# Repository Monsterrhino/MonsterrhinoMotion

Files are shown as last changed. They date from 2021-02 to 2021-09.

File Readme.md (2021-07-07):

# MonsterrhinoMotion

## Introduction
The MonsterrhinoMotion card is an independent stepper motor driver card to power and control up to 4 stepper motors that comes with a pre-installed firmware. The MonsterrhinoMotion card uses high quality stepper drivers (TMC5160) from Trinamic.
You can use Monsterrhino Motion in different ways depending on the complexity of your project: 

- Use the pre-installed library by sending commands **over a serial USB port** using a variety of predefined functions (see below)
- Use the pre-installed library by sending commands **over CAN bus** using a variety of predefined functions (see in the MonsterrhinoControl documentation)
- Program functions and actions with the **provided Arduino library** and upload directly to the card

In the simplest case all you need to do is **just connect 24V, a stepper motor and a USB cable** to the Monsterrhino Motion and you are ready to move the motor - **plug and play**.

The key features of the MonsterrhinoMotion stepper driver card are:

- up to 4 stepper motors
- two limit switches per motor
- encoder for each stepper motor
- up 12 digital inputs (24V)
- 1 digital output (24V)
- 3 PWM outputs (open collector)
- 2 CAN bus connector 
- USB C connector
- micro USB connector
- analog emergency power-off circuit that can be bridged with a jumper

## MonsterrhinoMotion pinout

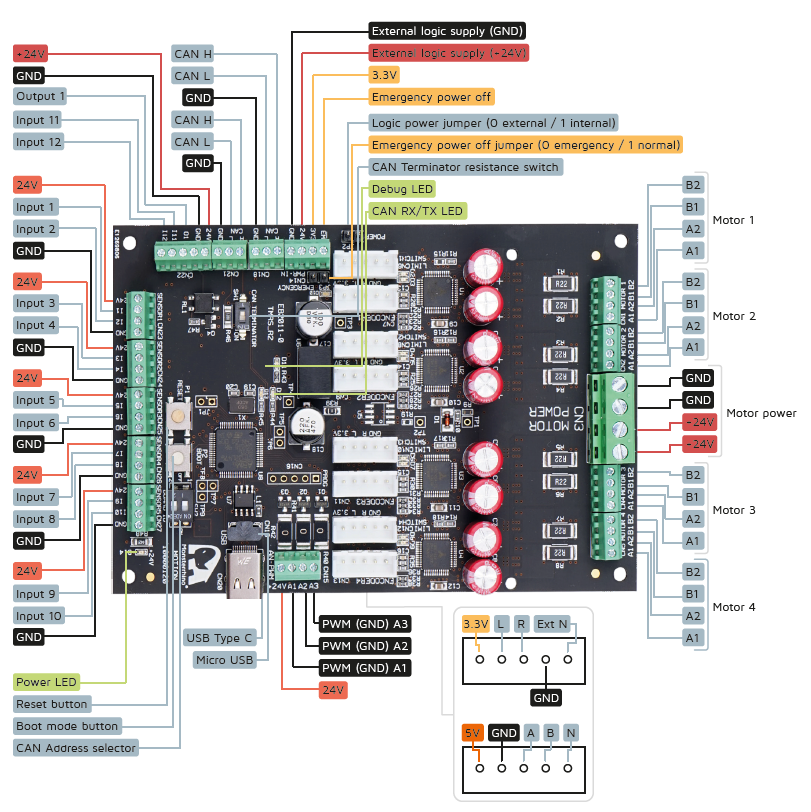
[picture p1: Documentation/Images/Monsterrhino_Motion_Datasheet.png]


## USB serial communication

### Connect to Monsterrhino Motion

Install the Arduino IDE on your computer (https://www.arduino.cc/en/software). Open the Arduino IDE on your computer. 

+ Select the right port under **Tools->Port** e.g. /dev/ttyACM0 or COM5. 
+ Open the serial monitor and set **115200 baud** and line ending to **Both NL & CR**. 

  <br><br>
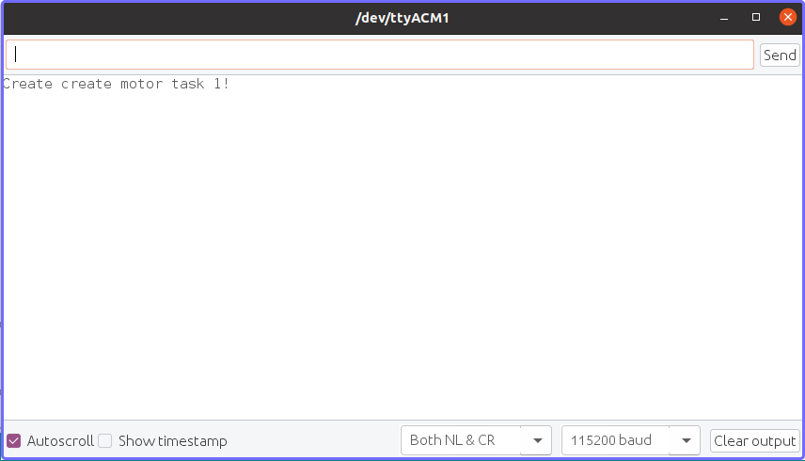
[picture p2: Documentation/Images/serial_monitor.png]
   
  <br><br>

Press the reset button on the Monsterrhino Motion than your ready to type your first command. If you have Motor 1 connected you can for example type: **m1mr 100** into the serial monitor and hit enter - now Motor 1 should move 1000 steps (that is 5 rotations - 200 steps per rotation or 1.8° per step). The meaning of this command is: **m1** - motor 1, **mr** move relative, **1000** - hundred steps. With **m1mr -1000** you can move 1000 steps into the other direction. 

(http://www.youtube.com/watch?v=Wm-6o_nRb1g "Serial communication")

### Commands
The MonsterrhinoMotion commands are combinations of commands from the list below. They are composed of the classifier: **m, i or f**. A number after the classifier letter selects the desired motor, input, or function: Motor 1 = **m1**, Userfunction 1 = **f1**. The classifier is followed by a function such as targetposition = **tp** and a number.

- **m1tp 100** - motor 1 move to target position 100
- **m4ma 200** - motor 4 set motor current to 200 mA
- **m3smp** - motor 3 save motor parameters
- **m2cp ?** - request motor 2 current position

The questionmark can generally be used to request a current value e.g. Motor 1 what is the current position = **m1tp ?**.

motor function |**subfunction**    |**subfunction** | values
---         | :-:     | :-: | :-:
TargetPosition |tp|targetpos |
CurrentPosition|cp|currentpos|
Rampmode|rm|rampmode |	p or positioning, v or velocity, h or hold
Motor current|ma|currentma |
MaxSpeed|ms|maxspeed |
CurrentSpeed|cs|currentspeed|
Register|r|register|
RampSpeeds|rs|rampspeeds|
Acceleration|ac|acceleration|
Accelerations|as|accelerations|
Stop|s|stop|
Enable|en|enable|
Disable|di|disable|
EncoderPosition|ep|encoderposition |
LatchedPosition|lp|latchedposition|
LatchedEncoderPosition|le|latchedencoder|
MotorDriveStatus|mds|motordrvstatus|
MotorRampStat|mrs|motorrampstat|
gStat|gs|gstat|
MotorCurrent|ma|currentma|
Freewheelingmode|fwm| freewheelingmode|
ModeChangeSpeeds|mcs| modechangespeeds|
Switch Mode|swm|swmode|
Save|sv|save|
SaveMotorParameter|smp|savemotorparameter|
Test|test|
Load|ld|load|
Startup|st|startup |

**input function**|subfunction|subfunction
---         | :-:     | :-:
InputFunction|if|inputfunction
StartUp|st|startup

**system function**|subfunction|subfunction
---         | :-:     | :-:
Start|s|start
Stop|t|stop
Variable|v|variable
Float|f|float
Startup|st|startup
Unlock|u|unlook

## Program the **Monsterrhinostep library** with Arduino IDE or VisualMicro

To use the the Monsterrhinosteb-Lib (https://github.com/Monsterrhino/MonsterrhinoMotion/tree/master/Library) library it is necessary to install following packages first:

## On Windows
Tested on Windows 10.

### Install Java Runtime Environment
If not already satisfied:

* Download the Java Runtime Environment from the official Website - https://www.java.com/en/download/manual.jsp 
* Install it by running the executable (.exe) file

### Prepare Arduino IDE:
* Download and install the Arduino IDE (Version 1.8.12) from the official page: https://www.arduino.cc/en/Main/Software (or get it from the Software folder)

* Start the Arduino IDE and add **Stm32duino** as follows:
  + Go to **File->Preferences**. Under the section **Additional Boards Manager URLs**:

       ```https://raw.githubusercontent.com/stm32duino/BoardManagerFiles/master/STM32/package_stm_index.json  ```  
       
**Note:** Please use exacatly this version, even if its deprecated
       
  <br><br>
  ![](Documentation/Images/additional_boards.png)     
  <br><br>
  
  + Go to **Tools->Board->Boards Manager** and search for **STM32 Cores**, choose version **1.8.0** and press *Install*. 
  
  <br><br>
  ![](Documentation/Images/boards_manager.png)    
  <br><br>
  
  After that you should be able to select **Nucleo-64** under **Tools->Board**. 

  <br><br>
  ![](Documentation/Images/nucleo64.png) 
  <br><br>
  
### Install STM32CubeProgrammer:
  
* Download **STM32CubeProgrammer** from the official page: https://www.st.com/en/development-tools/stm32cubeprog.html. You need to enter your email address for that. 
* Install it by running the executable (.exe) file.
* You can install it with the default settings. During the installation process, the drivers will be installed to.
* Verify the installation by opening the programm **STM32CubeProgrammer**. If the program opens normally, everything should be fine.

-----------------------------------------------------------------
**_Attention_:**
Check if you can open the **STM32CubeProgrammer** and connect to your MonsterrhinoMotion. Select USB and **bring your MonsterrhinoMotion into boot-mode** by pressing reset while holding down the boot button. After successfully connecting to your device you should see something similar to:

  <br><br>
  ![](Documentation/Images/stm32.png) 
  <br><br>

### Following files need to be replaced inside the Arduino folder
Replace following two files on your computer with the files you find inside the https://github.com/Monsterrhino/MonsterrhinoMotion/tree/master/Library/Replace folder:

  + Replace **usbd_cdc_if.c** inside:  
  ```C:\Users\username\AppData\Local\Arduino15\packages\STM32\hardware\stm32\1.8.0\cores\arduino\stm32\usb\cdc```
  **or**
  ```C:\Users\username\Documents\ArduinoData\packages\STM32\hardware\stm32\1.8.0\cores\arduino\stm32\usb\cdc ```  
   **-** depending on location of your installation (it could also be a different location). 
  
  + Replace **variant.c** inside:  
  ```C:\Users\username\AppData\Local\Arduino15\packages\STM32\hardware\stm32\1.8.0\variants\NUCLEO_L476RG ``` 
  **or**
  ```C:\Users\username\Documents\ArduinoData\packages\STM32\hardware\stm32\1.8.0\variants\NUCLEO_L476RG ```  
   **-** depending on location of your installation (it could also be a different location). 

### Add the **STM32duino_FreeRTOS.zip** to the Arduino IDE:
The **STM32duino_FreeRTOS.zip** can be found here: https://github.com/Monsterrhino/MonsterrhinoMotion/tree/master/Library. Download it and add **STM32duino_FreeRTOS.zip** to the Arduino IDE libraries from the menu **Sketch->Include Library->Add ZIP Library**.
  
### Add the **MonsterrhinoStep-Lib** to the Arduino IDE:
To add the **MonsterrhinoStep-Lib** to the Arduino IDE download the **MonsterrhinoStep-Lib.zip** from https://github.com/Monsterrhino/MonsterrhinoMotion/tree/master/Library and proceed with following steps:

* Open the Arduino IDE, for each libary inside the Libs folder go to **Sketch->IncludeLibrary->Add .ZIP Library ..** and select the **MonsterrhinoStep-Lib.zip** file.
* Open the Monsterrhino application in your Arduino IDE: **File->Examples->Monsterrhinostep->monsterrhinostep**.
  
  <br><br>
  ![](Documentation/Images/monsterrhinostep.png) 
  <br><br>
  
  Now you should see following files in the Arduino IDE: **monsterrhinostep**, **User_Functions1.cpp**, **User_Functions2.cpp**, **User_Functions3.cpp**, **User_Functions4.cpp**, **User_Functions5.cpp**, **User_Functions6.cpp**, **build_opt.h**.
  
  <br><br>
  ![](Documentation/Images/library.png) 
  <br><br>
  
* Before you can start you need to adjust some settings in the Arduino IDE under **Tools**:
  + Board: "Nucleo-64" **Tools -> Board .. -> STM32 Boards -> Nucleo-64**
  + Board part number: **Nucleo L476RG**
  + USB support (if available): **CDC (generic 'Serial' supersede U(S)ART-)**
  + Upload method: **STM32CubeProgrammer (DFU)** 
  
  <br><br>
  ![](Documentation/Images/settings.png) 
  <br><br>

### Upload your MonsterrhinoMostion application to your MonsterrhinoMotion card
  
For uploading a program, connect your computer to your MonsterrhinoMotion card via micro USB or USB C, push the reset button while holding down the debug button on your MonsterrhinoMotion card. You will hear the Windows USB connection sound twice. After successfully entering **boot mode** the debug LED will stop blinking.
Now you can hit the compile and upload button to upload the MonsterrhinoMotion application to the card. After the upload press the **reset button**.

### Set up Visual Studio to use with Monsterrhino
The setup of Arduino IDE shown before has to be completed prior to setting up Visual Studio.

* Download and install Visual Studio (https://docs.microsoft.com/en-us/visualstudio/install/install-visual-studio?view=vs-2019), add the workload **desktop development with c++** during the installation process. 
* Install Arduino Extension in Visual Studio: go to **Extension -> ManageExtensions -> Online**, search for **Arduino** and install **Arduino IDE for Visual Studio (Visual Micro)** (you will have to close Visual Studio during the installation process).
* Open the location configuration **Extensions -> vMicro -> General -> Configure Arduino IDE Location(s)** and enter the correct paths, it should look similar to the example in the image:  

<br><br>
![](Documentation/Images/config.jpg){width=50%}  
<br><br>

* Open VisualStudio and press **Continue without code** and then go to **File->Open->Arduino Project** and navigate to ```..\Arduino\libraries\Monsterrhinostep-Lib\examples\monsterrhinostep\monsterrhino.ino```
* Adjust the vMicro settings (**Extensions -> vMicro**) to the same values as you did in your Arduino IDE (see **adjust the Arduino IDE settings like follows** above)
* Open Visual Studio, open **Extensions -> vMicro -> ViewPortMonitor ** (Monsterrhino needs to be connected to your computer to be able to open it), switch the setting **line endings** to **Both CR & LF**
* You can now use the ViewPortMonitor to connect to your Monsterrhino and directly send commands 
* To use Visual Studio to compile and upload your code to your Monsterrhino, you first have to restart it in debug mode (keep debug button pushed while pressing the reset button)

## On Ubuntu 
Tested on Ubuntu 20.04. 

* Install the Arduino IDE (tested with version 1.8.12)
* In the Arduino IDE go to **Properties/Additional BoardsManager** and add following 

  ```https://github.com/stm32duino/BoardManagerFiles/raw/master/STM32/package_stm_index.json ```
  
* Under **Arduino/Boardsmanager** add ```stm32 cores```.
* Install the Java Runtime Environment by executing the following command in your terminal ```sudo apt install openjdk-8-jre```.
* Download and install the **STM32CubeProgrammer**. There might be problems with JavaFX, you can try this fix https://askubuntu.com/a/1316213.

  **Attention**
  Check if you can open the **STM32CubeProgrammer** and connect to your MonsterrhinoMotion. Select USB and bring your MonsterrhinoMotion into boot-mode by pressing reset while holding down the boot button. It might be usefull to open the **STM32CubeProgrammer** via the terminal, so you get some information if something is not right.
  
  **Note**
  If in your terminal you read something about **permission denied** it might be necessary to copy a rules.d file to the STM32 folder. To do so you can follow this instructions (taken from: https://community.st.com/s/question/0D53W000000aP9J/no-stm32-device-in-dfu-mode-connected): 
  
  * Make sure you have installed this library: ```sudo apt-get install libusb-1.0-0```
  * To allow STM32CubeProgrammer to access the USB port through low-level commands, proceed as follows: 
  ```cd $HOME/STM32MPU_workspace/STM32MPU-Tools/STM32CubeProgrammer-x.y.z/Drivers/rules```
  * Then execute: ```sudo cp *.* /etc/udev/rules.d/```
  * Restart the STM32CubeProgrammer 
  
  **After successfully connecting** to your device you should see something similar to:
  
    <br><br>
    ![](Documentation/Images/stm32.png) 
    <br><br>

* Replace following two files on your computer with the files you find inside the https://github.com/Monsterrhino/MonsterrhinoMotion/tree/master/Library/Replace     folder:

  + Replace **usbd_cdc_if.c** inside:  
  ``` /home/g/.arduino15/packages/STM32/hardware/stm32/1.8.0/cores/arduino/stm32/usb/cdc ```
  + Replace **variant.c** inside:  
  ``` /home/g/.arduino15/packages/STM32/hardware/stm32/1.8.0/variants/NUCLEO_L476RG ```
  
  * Add **Monsterrhinostep-Lib.zip** and **STM32duino_FreeRTOS.zip** to the Arduino IDE libraries from the menu **Sketch->Include Library->Add ZIP Library**.

* If you whant to use a **STM32nucleo** to program over **ST-Link** it might be necessary to give permission to the USB device (as described here: https://stackoverflow.com/questions/22713834/libusb-cannot-open-usb-device-permission-isse-netbeans-ubuntu): 
 ``` sudo chmod o+w /dev/bus/usb/123/456 ```

## Upload from STM32Cube

If you are not able to upload your project via the Arduino IDE you can try to upload the compiled project file with STM32Cube as follows:

* Compile your project in the Arduino IDE. Go to **->Sketch->Export compiled Binary**.

* Set your MonsterrhinoMotion in boot mode and connect it via STM32CubeProgrammer (see "Install STM32CubeProgrammer").

* Upload the compiled Hex-File to STM32CubeProgrammer with the task **->Open File** (next to Device memory).

* Press button **Download** to load your project to the device.

<br><br>
![](Documentation/Images/cubeProgrammer_upload.png) 
<br><br>

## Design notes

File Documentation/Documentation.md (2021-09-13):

---
title: "Monsterrhino Motion: Documentation and Examples"
output: 
  bookdown::html_document2:
    toc: true
    toc_float: true
    fig_caption: true
---
-->

<!-- ![](Images/Monsterrhino_Images/logo.png){width=20%} 

<p align="center">
  <img width="100" src="Images/Monsterrhino_Images/logo.png">
</p>

<p align="center">
  <img width="500" src="Images/Motion_Illustrated.png">
</p>
 -->
 
 <!-- 
 ![](Images/Reset_Boot.gif)
 
-->

# General
**Monsterrhino Motion** is an independent stepper motor controller.  

The MonsterrhinoMotion card can be controlled via three different ways: over **predefined USB commands**, over **predefined CAN commands** or by **programming the MonsterrhinoMotion card directly** using the Monsterrhinostep-Lib for the ArduinoIDE. 

It can run up to 4 stepper motors at once - in parallel. The powerful MCU combined with our advanced firmware (multitasking capable - up to 6 user tasks) allows you to control stepper motors in the most simple way - you can program it with the Arduino IDE or with more advanced IDEs. Our firmware allows you to program the card at a high level e.g. you tell the motor to rotate continuously, make a 100 steps, etc. Further key features are limit switch connectors for each motor, encoder connectors, digital sensor inputs and digital/analog outputs. 
The CAN interface offers reliable high performance communication with other devices such as Monsterrhino Motion, Monsterrhino Control, Raspberry Pi, Arduino and many more.

Specification:  

- **4** stepper motors
- **12** digital inputs
- **1** digital output (with load)
- **3** analog outputs
- **1** emergency jumper/switch

## Modes
As shown above, the Motion has two modes.  

-**Normal mode:** After a reset (press button P1 once) the Motion is in normal mode and the serial LED (D11) is blinking (existing USB-connection required).  
-**Boot mode:** This mode allows you to program the Motion.  

This animation shows you how to enter in these different modes:



## Communication
The board offers two main types of communication:  

* **Serial:** U(S)ART with USB is used to communicate with lower speed.
* **CAN:**  CAN (common in automotive) is used to communicate faster and without failure.

# USB
U(S)ART is the simplest way to give commands. MonsterrhinoMotion can be controlled directly, out of the box, via U(S)ART-communication.  

Just open the serial command window and select the following settings and the COM-port of your MonsterrhinoMotion.  
After a successful connection with your MonsterrhinoMotion you can send commands as shown here:  
(**Attention:** Motion needs to be in normal mode **not** boot mode! Led is blinking)
```
m1tp 100  (Motor 1 target point 100 steps)
m3mr 200  (Motor 3 move relative 200 steps)
m2ma 100  (Motor 2 set motor current to 100mA)

m3ma ?    (Motor 3 returns motor current in mA)
m2cp ?    (MOtor 2 returns current position)
```
**Note:** A list of all UART-commands can be found in the following chapter [Serial U(S)ART].

## Setup

### Arduino - Serial commands
First install the Arduino IDE on your computer. Open the Arduino IDE and connect the MonsterrhinoMotion card via USB cable. Supply the MonsterrhinoMotion with 24V, now you should see the green power indicator LED permanently shine. After plugin in the USB to the computer and pressing the Reset button on the MonsterrhinoMotion a second green LED should start blinking.

In the Arduino IDE select the port of your MonsterrhinoMotion, if the MonsterrhinoMotion is the only device you have connected to your computer you should see only one device in your list:
<br>

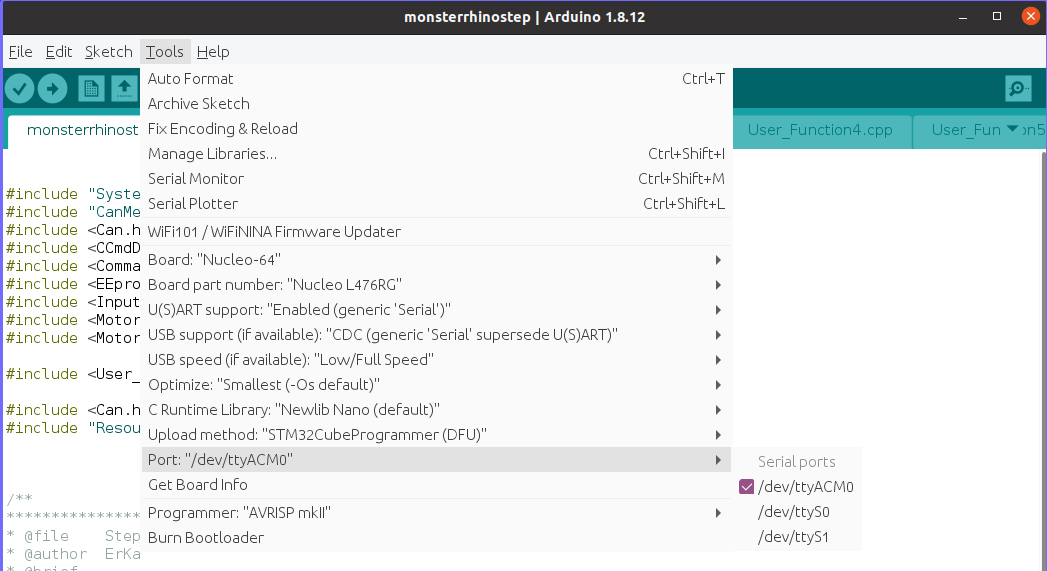
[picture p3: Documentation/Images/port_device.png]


<br>
After choosing the correct device you should see it in the menu e.g. **Port: "/dev/ttyACM0"** on Linux or **Port: "COM3"** on Windows.
<br>

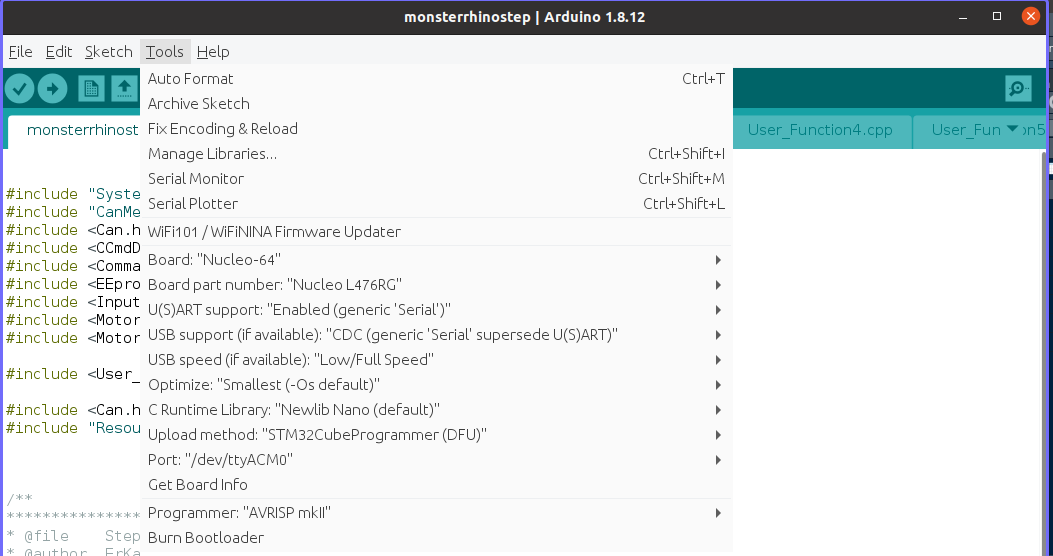
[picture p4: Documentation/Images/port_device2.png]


<br>
Now open the **Serial monitor** of Arduino by clicking on the **magnifying glass** symbol.
<br>

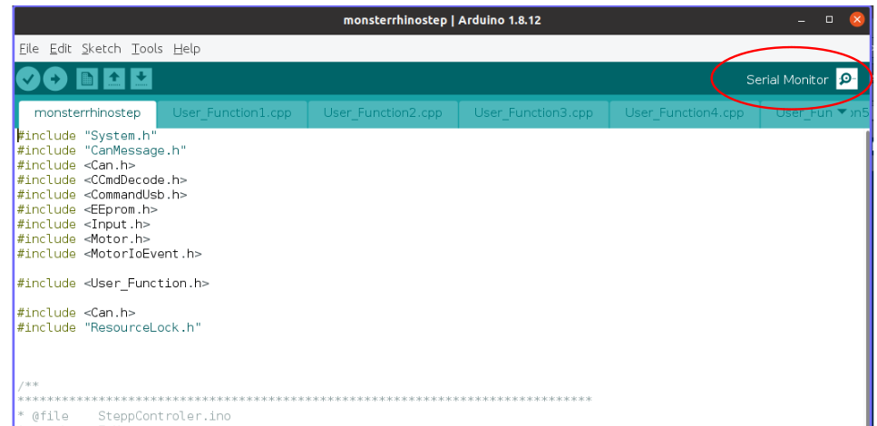
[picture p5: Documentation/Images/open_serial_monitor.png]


<br>
In the serial monitor window adjust following settings: 

* Line ending: Both CR & LF
* Baud rate: 115200
<br>

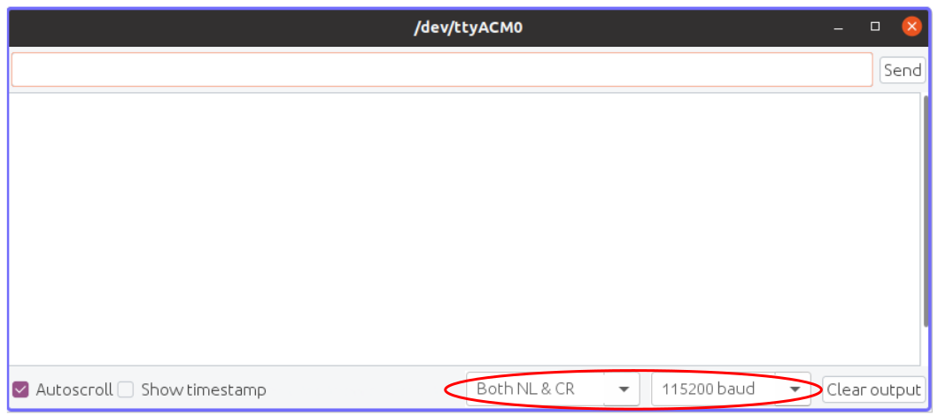
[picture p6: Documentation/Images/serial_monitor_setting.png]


### Python - Serial commands

Here we show an example of how Python can be used to send serial commands to the MonsterrhinoMotion card. 
First you need to make sure you have **Python3** and the package **pyserial** installed. 

Following minimal example shows you how to interact with the MonsterrhinoMotion card using Python.

As first step in your Python program you need to import the pyserial package:

```Python
import serial, time
```

Setup and open the serial port:

```Python
ser = serial.Serial()
# ser.port = '/dev/ttyUSB0'
ser.port = 'COM3'
ser.baudrate = 115200
ser.bytesize = serial.EIGHTBITS  # number of bits per bytes
ser.parity = serial.PARITY_NONE  # set parity check: no parity
ser.stopbits = serial.STOPBITS_ONE  # number of stop bits
# ser.timeout = None          #block read
ser.timeout = 1  # non-block read
# ser.timeout = 2              #timeout block read
ser.xonxoff = False  # disable software flow control
ser.rtscts = False  # disable hardware (RTS/CTS) flow control
ser.dsrdtr = False  # disable hardware (DSR/DTR) flow control
ser.writeTimeout = 2  # timeout for write

# open COM port
ser.open()
```

Now you can define a function to send serial commands to the MonsterrhinoMotion:

```Python
def write_to_Monsterrhino(cmd):
        if ser.isOpen:
            print("Write: " + str(cmd))
            message = "{}\n\r".format(cmd)
            print(message)
            ser.write(str.encode(message))
```

Using this function you can send for example a command to move relative 400 steps:

```Python
write_to_Monsterrhino("m1mr 400")

```

After you completed the operations close the serial port by issuing following command:

```Python
ser.close()

```

## Serial commands

U(S)RT is the simplest way to give commands. MonsterrhinoMotion can be controlled directly, out of the box, via U(S)ART-communication.  

Just open the serial command window and select the following settings and the COM-port of your MonsterrhinoMotion.  
After a successful connection with your MonsterrhinoMotion you can send commands as shown here:  

Serial communication is possible via USB. The following properties should be set to ensure correct data transfer:

* U(S)ART support: generic 'Serial'
* Line ending: Both CR & LF
* Baud rate: 115200

The serial command is build as follows:  

function + Nr + subFunction (+optional: value/subFunction2 + value)

```
m1tp 100  (Motor 1 target point 100 steps)
s reset
m1rm v    (Motor 1 ramp mode set to velocity)
m3rs ?    (Prints ramp speeds in the command window)
```
**Attention:** Motion needs to be in normal mode **not** boot mode! Led is blinking

### Motor commands

function|subfunction1|subfunction1|subfunction2/value
-|--|---         |-----
m|tp  |targetpos         |(value) or (?)
m|cp  |currentpos        |(value) or (?)
m|rm  |rampmode          |v,p,h or (?)
m|ms  |maxspeed          |(value) or (?)
m|cs  |currentspeed      |(?)
m|r   |register          |Controller Register?
m|rs  |rampspeeds        |(3 values: start,stop,hold), (?) for more information
m|ac  |acceleration      |(value) for A1,Amax,D1,Dmax, (?) for more information
m|as  |accelerations(    |(5 values: A1,D1,hold,Amax,Dmax), (?) for more information
m|s   |stop              |(value) TODO: no output in serial and afterwards problems
m|en  |enable            |(value) or (?)
m|ep  |encoderposition   |TODO
m|lp  |latchedposition   |TODO
m|le  |latchedencoder    |TODO
m|mr  |moverelative      |(value)
m|mds |motordrvstatus    |(?), other functions to set/get drive status
m|mrs |motorrampstat     |(?), other functions to set/get ramp status
m|gs  |gstat             |(?), other functions
m|ma  |currentma         |(value) or (?)
m|fwm |freewheelingmode  |1,0 or (?)
m|mcs |modechangespeeds  |(3 values: pwmThrs, coolThrs, highThrs)
m|swm |swmode            |(?), other functions with value afterwards (s.a. LimitSW section)
m|cc  |coolconf          |(?), other functions
m|smp |savemotorparameter|-
m|iv  |icversion         |(?)
m|ld  |load              |default or defaultall TODO:?
m|st  |**startup**           |(?), other functions to set/get startup values **see 2.1.2**
m|ho  |homing            |(?), other functions to set/get homing values
m|tsc |tunesteathchop    |-
m|tps |tunestallguard    |-

### Startup (st) parameter

Parameter | aberration
:---|:--:
drvStrength | drs
bbmTime | bt
bbmClks | bc
SenseResistor | sr
MotorCurrent | mA
MotorCurrentReduction | mAr
Freewheeling | fwm
Iholddelay | ihd
PwmOfsInitial | poi
PwmGradInitial | pgi
StepperDirection | sd
MotorSteps | mst
PWMThrs | pt
COOLThrs | ct
HighThrs | ht
SWMode | swm
RampMode | rm
RampMaxSpeed | ms
RampSpeedsStart | rms
RampSpeedsStop | rmt"
RampSpeedsHold | rmh"
AccelerationsAMax | AMax"
AccelerationsDMax | DMax"
AccelerationsA1 | A1"
AccelerationsD1 | D1"
CoolConf | CC"
EncoderResolution | er"
EncoderAlloweddeviation | ead"
EncoderSetup | es"
EncoderInverted | ei"
HomingMode | hm"
HomingOffset | ho
HomingMaxPos | hp
HomingTimeout | ht
HomingSpeed_2 | hs2
HomingDmax | hd

For example if you whant to invert the rotation direction of the stepper motor 1 you can execute following commands:
```C++
m1st sd ?
```
This returns you e.g. **Get Startup:   StepperDirection: 1**. Now you can change the direction by executing:
```C++
m1st sd 0
m1smp
```
Reset the card and the motor will spin now in the opposite direction.

### Input commands

```
i1v ?
i5st ?
```

function|subfunction1|subfunction1|subfunction2
-|--|---         |-----  
i|if  |inputfunction     |(?)
i|st  |startup           |(?)
i|v   |value             |(?)

### System commands

```
s reset   (Resets the controller)
s pw1 125 (Sets analog port 1 to half power)
s ca ?    (Returns can adress)
```

function|subfunction1|subfunction1|subfunction2
-|--|---         |-----  
s|sv  |softwareversion   |(?)
s|hv  |hardwareversion   |(?)
s|o   |output            |(?), (value) (0=OFF;1=ON;3=TOGGLE)
s|bi  |bordid            |(?) according to SW2, binary [0-3]
s|ft  |firmwaredaytime   |(?) return compile time
s|st  |startup           |(?), other functions to set/get startup system values
s|pw  |pwm +[AnalogPort] |(value) [0-255]
s|pf  |pwmfrequency + [Aport]|(value)
s|sv  |save              |-
s|reset|reboot           |-
s|ca  |canadress         |(value),(?)
s|cs  |canspeed          |(value),(?)
s|ld  |load              |-
s|d   |debug             |-

### Userfunction commands

function|subfunction1|subfunction1|subfunction2
-|--|---         |-----  
f|s  |start   |(value)
f|t, b  |stop, break   |(value)
f|v  |variable  |(?)(value)
f|f  |float  |(?)(value)
f|st  |startup |(value)
f|u  |unlock |(value)

# Programming

**_ATTENTION_**:
To use this feature of the MonsterrhinoMotion card make sure you installed the requirements as described here: https://github.com/Monsterrhino/MonsterrhinoMotion

Follow the instructions under section: **Program the Monsterrhinostep library with Arduino IDE or VisualMicro**.

<br>

It is possible to program various functions on the MonsterrhinoMotion, this enables a fully autonomous and dynamic system.  
The main structure of the code consists of six "UserFunction" files (User_Function1.cpp) and the main file ("monsterrhinostep.ino").  

The following image shows you the **main structure** of the files used to program the Motion:

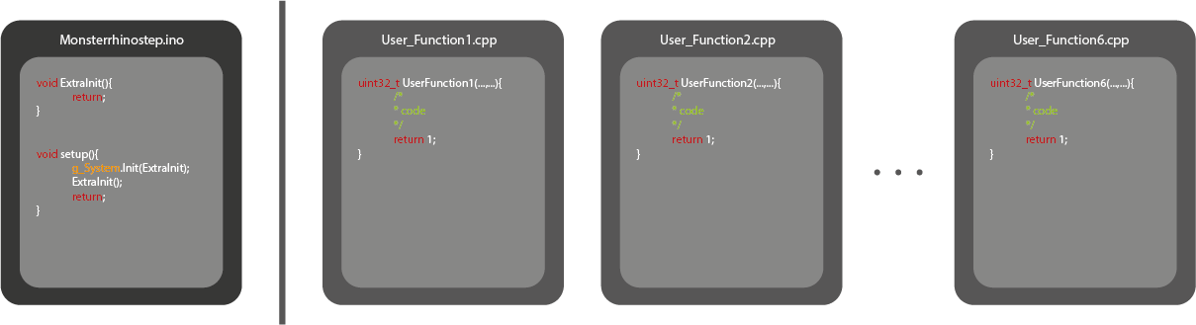
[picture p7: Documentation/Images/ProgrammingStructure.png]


**Note:**
- The code is almost **fully documented** with doxygen in the Html-file "" on Github. See that file for more detailed information.
- MonsterrhinoMotion **runs on Arduino but is not the same programming concept.**  
- The loop function is **not used**, because all processes and actions are programmed in the "Userfunctions" that can be executed simultaneously.

## "monsterrhinostep.ino"-file
This file is used for main initialization.  
Example:
```C++
#include <Wire.h>
#include  "PortIni.h"

void ExtraInit()
{
	g_Input1.SetRunRisingFunction(INPUT_RUN_USERFUNCTION_START_2 + 1);
	//set Input1 interrupt at rising edge, Start userfunction 2 with parameter par=1
}
//------------------------------------------------------------------------------
void setup() {
	// Init IO
	g_System.Init(ExtraInit);
	ExtraInit();
}
```

## User Function
The six "*UserFunction*"-files can be programmed for any action. They can be started and stopped in parallel with inputs, CAN-commands, UART-commands or other *UserFunctions*.  

Serial:
```
f1s1
//Start UserFunction1 with parameter par=1
f2s2
//Start UserFunction2 with parameter par=2 (even if function1 is not finished)
f1t
//Stop UserFunction1
```

Functions to start or stop other UserFunctions are:

Code:
```C++
g_UserFunction[0].TriggerStart(2)
//Start UserFunction 1 with par 2
g_UserFunction[3].TriggerStart(0)
//Start UserFunction 4 with par 0
```

## Motor control

### Motor setup
*(~/ExamplesCpp/Example1_MotorSetup.cpp)*

To run a stepper motor, first you need to set up the main motor parameters such as motor current, speed, acceleration and others. Otherwise default values are used. 
As you can see in the following code a task needs to start in one of the six "UserFunctions":  

```C++
void MotorInit()
{
	g_Motor1.LoadMotorParameter();		
	//Loads default motor values (SenseResitor, Current, ...)

	g_Motor1.SetMotorCurrent(100);		//Motor current in mA (0.001 Ampere)
	g_Motor1.SetMotorCurrentHold(50);	//Motor standstill current

	g_Motor1.Begin();					        				

	g_Motor1.ResetRampStatus();			  //Reset RampStatus flags and set ramp Speed/Acceleration to default
	g_Motor1.SetRampSpeeds(g_Motor1.GetStartup_RampSpeedsStart(),             g_Motor1.GetStartup_RampSpeedsStop(), g_Motor1.GetStartup_RampSpeedsHold()); //Start, stop, threshold speeds
	g_Motor1.SetAccelerations(g_Motor1.GetStartup_AccelerationsAMax(), g_Motor1.GetStartup_AccelerationsDMax(), g_Motor1.GetStartup_AccelerationsA1(), g_Motor1.GetStartup_AccelerationsD1());
	
	return;
}

uint32_t UserFunction1(uint32_t par, UserFunction* pUserFunction)
{
  MotorInit(); //Motor initialization
  return 1;
}
```
**Note:** It is recommended to use the function ```g_Motor1.ResetRampStatus();``` before a motor action. Otherwise some flags could be set and the motor wont react.	

In the following examples the function "MotorInit" is used but not shown.  

### Ramp behavior

With the ramp behavior parameters you can adjust the specifications of your motor:  

* **Acceleration A1:** Start acceleration
* **Acceleration Amax:** Maximum acceleration
* **Deceleration D1:** Start deceleration
* **Deceleration Dmax:** Maximum deceleration
* **RampSpeed V1:** Acceleration phase speed
* **RampSpeed Vmax:** Maximum speed (after acceleration phase)
* **RampSpeed Vmax:** Deceleration phase end speed (motor stops)
* **MaxSpeed:** Maximum motor speed in steps/s (0-?) TODO

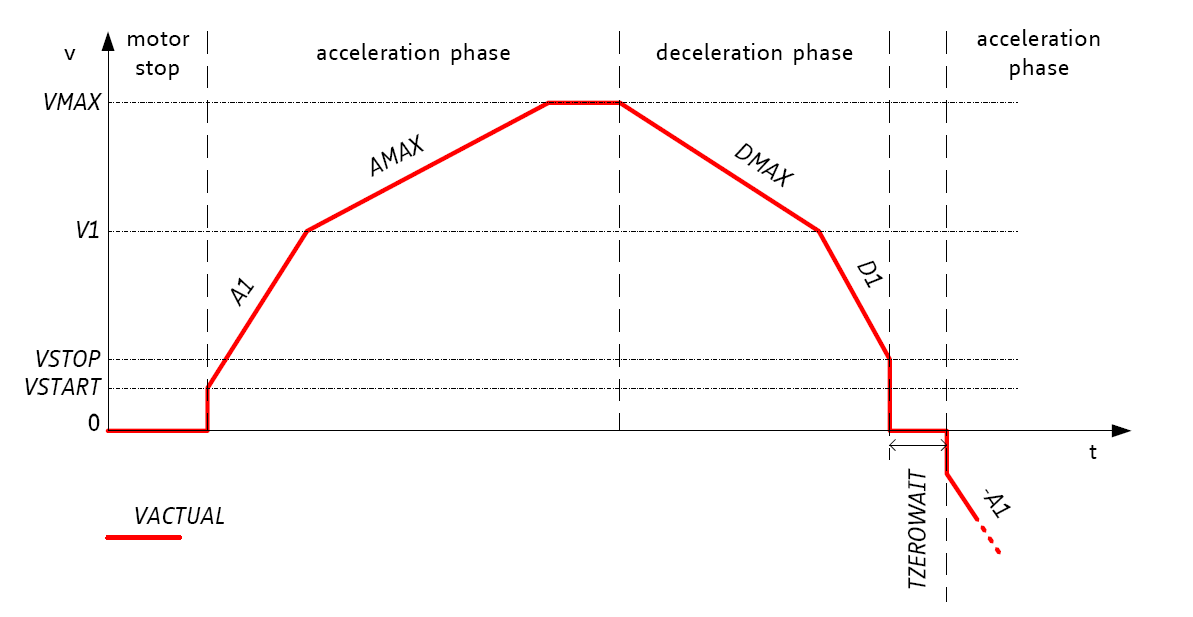
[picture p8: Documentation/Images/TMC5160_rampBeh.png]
Ramp behaviour (Datasheet TMC5160/A)


An example to set these parameters (with the startup values) is shown here.
```C++
g_Motor1.SetRampSpeeds(
g_Motor1.GetStartup_RampSpeedsStart(), g_Motor1.GetStartup_RampSpeedsStop(), g_Motor1.GetStartup_RampSpeedsHold()
); //V1,VMAX, VSTOP

g_Motor1.SetAccelerations(
g_Motor1.GetStartup_AccelerationsAMax(), g_Motor1.GetStartup_AccelerationsDMax(), g_Motor1.GetStartup_AccelerationsA1(), g_Motor1.GetStartup_AccelerationsD1()
); //AMAX, DMAX, A1, D1
```

**Note:** Value *Vstart* is default zero.  
**See also:** Serial [Motor commands] ramp mode (*m1rs,m1rc, m1as*)

### Ramp mode
```C++
g_Motor1.SetRampMode(MotorClass::RampMode::POSITIONING_MODE);
g_Motor1.SetRampMode(MotorClass::RampMode::VELOCITY_MODE);
g_Motor1.SetRampMode(MotorClass::RampMode::HOLD_MODE);
```

There are three different ramp modes:  

* **[Positioning mode]:** Motor turns til it reached its target point.  
* **[Velocity mode]:** Motor velocity to max speed.
* **[Hold mode]:** Velocity remains unchanged, unless stop event occurs. 

**See also:** Serial [Motor commands] ramp mode (*m1rm (v,p,h or ?)*)

#### Positioning mode

Set motor to positioning mode:
```C++
g_Motor1.SetRampMode(MotorClass::RampMode::POSITIONING_MODE);
```

This mode allows you to move a defined number of steps.

* **TargetPosition**: this mode moves to the given position e.g. if the motor is on position 100 and you set ``` g_Motor1.SetTargetPosition(-200.0);  ``` the motor will automatically move -300 steps to the position -200. If the motor is on position -100 and you set ``` g_Motor1.SetTargetPosition(-200.0);  ``` the motor will move -100 stepps.

* **MoveRelative**: this mode moves the motor indipendent of the current position e.g. if the motor is on position 100 an you set   ``` g_Motor2.SetMoveRelative(40);``` it will move to position 140. If you repeat the command again you will move to position 180.

##### Non blocking move
If it is intendet that the program continous while the motor moves to a given position you can simply use this commands: 
```C++
g_Motor1.SetTargetPosition(200.0);  
//Set target position to 200 steps (double value)
g_Motor1.SetMoveRelative(10.0);     
//Set target position 10 steps relative from current position
```

The same works also in negative direction:
```C++
g_Motor1.SetTargetPosition(-200.0);  
//Set target position to -200 steps (double value)
g_Motor1.SetMoveRelative(-10.0);     
//Set target position -10 steps relative from current position
```
##### Blocking move
If you want to pause your program until the movement of a motor has finished you can do that as follows:
```C++
g_Motor2.SetMoveRelative(40);
pUserFunction->m_MotorIoEvent.SetOrCondition(MOTORIOEVENT_MOTOR2PosReached);  // waits until the target position has reached 
if (pUserFunction->WaitEvent() == USERFUNCTIONEVENT_EXIT) return false;       // waits until the target position has reached
```
This also works with moving to an absolute position:
```C++
g_Motor2.SetTargetPosition(-200.0);
pUserFunction->m_MotorIoEvent.SetOrCondition(MOTORIOEVENT_MOTOR2PosReached);  // waits until the target position has reached 
if (pUserFunction->WaitEvent() == USERFUNCTIONEVENT_EXIT) return false;       // waits until the target position has reached
```
However for going to an absolute position you can also use the one-liner:
```C++
if (pUserFunction->SetTargetPosition_MotorWait(g_Motor2, -30.0f) == USERFUNCTIONEVENT_EXIT) return false;
```

#### Velocity mode  
In this mode the motor turns with the maximum speed.
```C++
g_Motor1.SetRampMode(MotorClass::RampMode::VELOCITY_MODE)
//Set ramp mode to "VelocityMode"
g_Motor1.SetMaxSpeed(100);
//Set maximum speed to 100 steps/sec
```

**Note:** When changed to this mode, max speed is zero. To begin set **max speed** to a value greather than 0.  

### Move to sensor

Sometimes you want to move a motor until you get a signal from a sensor or switch (like when you do homing), but afterwards you want to ignore the sensor signal (and cross the sensor) you can do that with following lines of code (moves motor 2 until the input 1 is pulled down):

```C++
g_Motor2.SetMaxSpeed(100);
g_Motor2.SetTargetPosition(10000);
pUserFunction->m_MotorIoEvent.SetOrCondition(MOTORIOEVENT_INPUT1_RisingHigh);
if (pUserFunction->WaitEvent() == USERFUNCTIONEVENT_EXIT) return false;
  
g_Motor2.SetCurrentPosition(0.0f);
g_Motor2.SetTargetPosition(0.0f);

```

### Motor stall detection

The MonsterrhinoMotion card can detect **motor stall** by measuring the back EMF (electro magnetic force) of the stepper motor. This is a useful feature for certain applications such as colaborative robots. Our library makes it relatively simple to implement this feature into your application, following function starts motor 1 with in the stall detection mode: 

```C++
uint32_t RunStallGuard(UserFunction *pUserFunction){
   
    g_Motor1.SetRampMode(MotorClass::VELOCITY_MODE);
    TMC5160_Reg::COOLCONF_Register coolconf = g_Motor1.GetCOOLCONF();
    TMC5160_Reg::SW_MODE_Register swMode = g_Motor1.GetSW_Mode();
    g_Motor1.SetMaxSpeed(run_speed);
    g_Motor1.SetModeChangeSpeeds(0, 50, 0);
    coolconf.sgt = 5; // Value from -64 .. 63. This value needs to be adjusted acording to your desired motor stop point 
    g_Motor1.SetCOOLCONF(coolconf);
    swMode.sg_stop = 1;
    vTaskDelay(1000);
    g_Motor1.SetSW_Mode(swMode);
    Serial.println("SG Active Left!");
   
    return 1;
  
}

```
The correct operation depends on the setting of the ```coolconf.sgt ``` factor, motor current setting, and motor speed setting. This settings have to be tuned for a correct functioning of this feature. The motor stall feature works only with ```SetRampMode(MotorClass::VELOCITY_MODE)```, due to the need of a steady motion of the motor in order to measure the back EMF.

The relative force measured on the stepper motor can be requested using following function:  

```C++
uint32_t TuneStallGuard2View(UserFunction *pUserFunction)
{

      TMC5160_Reg::DRV_STATUS_Register drvStatus = { 0 };
      drvStatus = g_Motor1.GetDrvStatus();
      
      return drvStatus.sg_result;
}

```
A fully working example of this function can be found here: https://github.com/Monsterrhino/MonsterrhinoMotion/tree/master/Documentation/ExampleCpps/DetectMotorStall

Simply open your ArduinoIDE and go to **Files->Examples->Monsterrhinostep->monsterrhinostep** and open the library example. Copy and past the content of **monsterrhinostep**, **User_Function1**, and **User_Function2** of the DetectMotorStall example to the acording files in your ArduinoIDE, compile and upload to the MonsterrhinoMotion card and enjoy.

### Hold mode

In this mode velocity remains unchanged, unless a stop event occurs.
If you change velocity after ramp mode was set to hold mode nothing happens.

Set motor to positioning mode:
```C++
g_Motor1.SetRampMode(MotorClass::RampMode::HOLD_MODE);
```

## Startup parameters

Motors have various values that are set default after reset.  
These values can be set with serial [Motor commands] or in the code. After you change one of the startup values you need to **save** the parameters with the serial command "s save".  
The command "m1st ?" returns a list of all parameters.

```
Serial commands:
m1st sr 100   
//Set motor1 startup value of senseResisor to 100 Ohm
s save        //System save
```

In the following list you can find all motor startup values. They can be read or set with these two functions:
**SetStartup_** or **GetStartup_**  
```C++
g_Motor1.SetStartup_SenseResistor(200);
//Set startup value for motor1 senseResistor to 200 Ohms
```

Function|Description
---|------
drvStrength           |
bbmTime               |
bbmClks               |
SenseResistor         |Resistor for current measuring in mOhm
MotorCurrent          |Motor current in mA
MotorCurrentReduction |
Freewheeling          |Reduce motor current to 0mA in standstill
Iholddelay            |
PwmofsInitial         |
PwmGradInitial        |
StepperDirection      |Direction of stepper motor
MotorSteps            |Full steps of stepper motor
PWMThrsInt            |
PWMThrs               |
COOLThrsInt           |
COOLThrs              |
HighThrs              |
HighThrsInt           |
SWMode                |see [Limit switch]
RampMode              |see [Ramp mode]
RampMaxSpeed          |Vmax ([Ramp behavior])
RampMaxSpeedInt       |Vmax integer ([Ramp behavior])
RampSpeedsStartInt    |Vstart integer ([Ramp behavior])
RampSpeedsStart       |Vstart ([Ramp behavior])
RampSpeedsHoldInt     |V1 integer ([Ramp behavior])
RampSpeedsHold        |V1 ([Ramp behavior])
RampSpeedsStopInt     |Vstop integer ([Ramp behavior])
RampSpeedsStop        |Vstop ([Ramp behavior])
AccelerationsAMaxInt  |Maximal acceleration integer
AccelerationsAMax     |Maximal acceleration
AccelerationsDMaxInt  |Maximal deceleration integer
AccelerationsDMax     |Maximal deceleration
AccelerationsA1Int    |Initial acceleration integer
AccelerationsA1       |Initial acceleration
AccelerationsD1Int    |Initial deceleration integer
AccelerationsD1       |Initial deceleration
HomingMode            |See parameter "mode" in [Homing]
HomingOffsetInt       |Homing offset integer
HomingOffset          |Homing offset
HomingMaxPos          |Homing max. position
HomingTimeout         |Homing timeout
HomingSpeed2Int       |Homing speed second contact integer
HomingSpeed2          |Homing speed second contact
HomingDmaxInt         |Homing max deceleration integer
HomingDmax            |Homing max deceleration
COOLCONF              |
                      |
EncoderResolution     |
EncoderAlloweddeviation|
EncoderSetup          |
EncoderInverted       |

## Limit switch

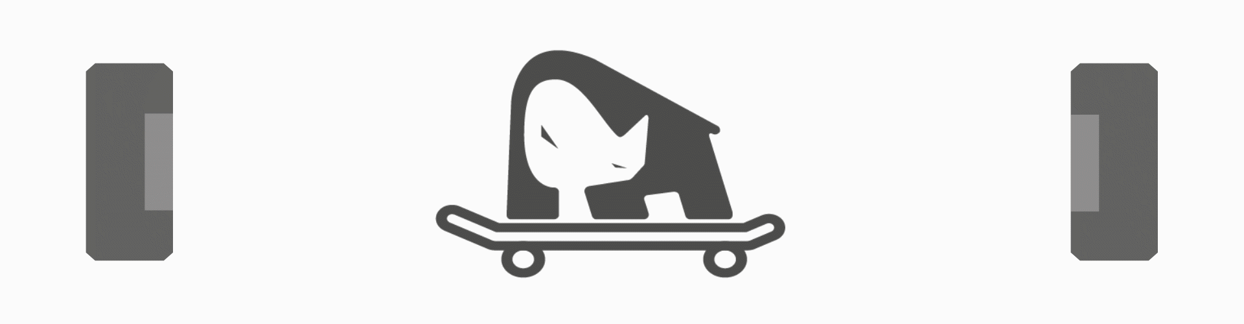
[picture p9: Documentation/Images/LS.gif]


It is possible to use two types of limit sensing:  

* **Limit switch:** Two limit switches per motor, can be of any type (mechanical, inductive, ...).  
Connection through the corresponding JST-XH connector CN[6,8,10,12] (for Motor 1,2,3,4)  
* **Sensorless:** The motor stops at a set force on the motor shaft.

Properties for motor limit switch configuration are set with following parameters:  

* **stop_l_enable:**  Enable automatic motor stop during active left reference switch input
* **stop_r_enable:**  Enable automatic motor stop during active right reference switch input
* **pol_stop_l:** Sets the active polarity of the left reference switch input (1=inverted, low active, a low level on REFL stops the motor)
* **pol_stop_r:** Sets the active polarity of the right reference switch input (1=inverted, low active, a low level on REFR stops the motor
* **swap_lr:**  Swap the left and the right reference switch inputs
* **latch_l_inactive:** Activate latching of the position to XLATCH upon an inactive going edge on REFL
* **latch_r_inactive:** Activate latching of the position to XLATCH upon an inactive going edge on REFR
* **latch_l_active:** Activate latching of the position to XLATCH upon an active going edge on REFL
* **latch_r_active:** Activate latching of the position to XLATCH upon an active going edge on REFR
* **en_latch_encoder:** Latch encoder position to ENC_LATCH upon reference switch event
* **sg_stop:** Enable stop by stallGuard2 (also available in dcStep mode). Disable to release motor after stop event.
* **en_softstop:** Enable soft stop upon a stop event (uses the deceleration ramp settings)

Example:  
```
Serial commands:
m1swm sle 1   
//Motor1 stop left enable
m1swm sre 1   
//Motor1 stop right enable
m1tp 10000
//Motor turns to targetPos 10000
//if the right limit switch is activated the motor stops (position not reached!)
```
or  
```C++
TMC5160_Reg::SW_MODE_Register swMode;
swMode.stop_l_enable = 1;
//stop left enable
swMode.stop_r_enable = 1;
//stop right enable
g_Motor1.SetSW_Mode(swMode);
//set selected options for motor1 swMode

g_Motor1.SetTargetPosition(1000);
//Set target position to 1000
```

## Homing

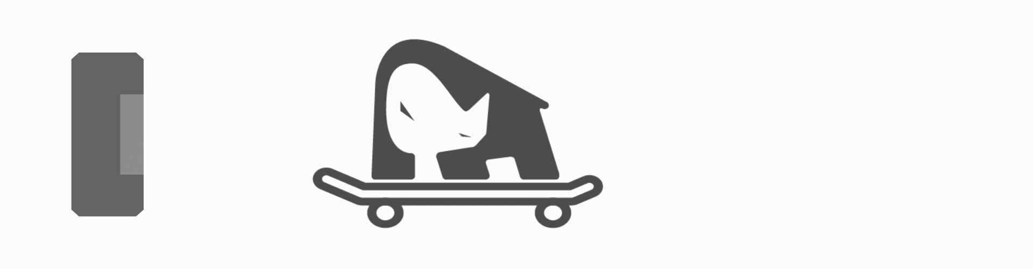
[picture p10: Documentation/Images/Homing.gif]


Homing has four main steps:  

1) **First contact** with limit switch  
2) Get **safety distance**: Go away 50 steps from first contact (with changed direction)  
3) **Second contact** with **slower** speed (*rampSpeed_2*)  
4) **Offset** after second contact (*homingOffset*, with changed direction)  

Homing can be configured with the following parameters:  

```C++
g_Motor1.m_HomingParameters.mode = 1;
g_Motor1.m_HomingParameters.rampSpeedHold = 200.0;
g_Motor1.m_HomingParameters.homingOffset = 15.0;
```  
* **mode:** homing on the **left (1)** or **right (2)** side or **both sides (3)**. 0 is homing off.
* **timeOut:** Timeout without successful homing
* **maxPos:** Maximal position without successful homing  (in microsteps)
* **rampSpeed:** Initial speed in homing (step 1); default is Default_Startup_MaxSpeed
* **rampSpeed_2:** Speed in step 3: second contact
* **homingOffset:** Offset from actual switch position
* **rampSpeedStart:** 
* **rampSpeedStop:**  
* **rampSpeedHold:**  
* **accelerationsAmax:** Maximum acceleration
* **accelerationsDmax:**  Maximum deceleration
* **accelerationsA1:**  Start acceleration
* **accelerationsD1:**  Finish deceleration
* **multiple_homing:** Default "true", if "false" steps 2 & 3 are skipped

**Note:**  
In step 2, if switch is still pressed after 50 steps, this step will repeat.  
In step 3, motor turns 100 steps til it reaches the limit switch, otherwise there is a homing error.  
The motor gets set in POSITIONING MODE when homing. 

### Normal homing
When setting the "MOTOR_FUNCTION_HOMING" start-trigger, the motor begins homing with the **pre-selected** parameters.  
The next command is to keep the motor locked until the homing event is finished.  

```C++
g_Motor3.MotorFunction_TiggerStart(MOTOR_FUNCTION_HOMING);
pUserFunction->MotorHomingOk(LOCK_MOTOR3, par);
```

### Parallel homing

It is possible to home multipe axis in parallel or simultaneously. Following code homes for example **Motor1** and **Motor2**:

```C++
g_Motor1.ResetRampStatus();   // Resets the limit switch register
g_Motor2.ResetRampStatus();   

g_Motor1.MotorFunction_TiggerStart(MOTOR_FUNCTION_HOMING);    // Starts homing on motor1
g_Motor2.MotorFunction_TiggerStart(MOTOR_FUNCTION_HOMING);    // Starts homing on motor2

pUserFunction->MotorHomingOk(LOCK_MOTOR1 | LOCK_MOTOR2, par);   // Waits for motor 1 und motor 2 to finish homing
```

This methodology allows to home all four axis of the MonsterrhinoMotion card in parallel. An example of multiple axis homing can be seen here: 

https://www.youtube.com/channel/UCkQM9dfGWviW-XfwOgTvgYg

### Sensorless homing
It is also possible to home without limit switches using the motor stall detection feature. Example code is provided in the section **Motor stall detection**. The function 
is presented in following video:  

https://www.youtube.com/watch?v=vMpDnNlyOfQ

## Digital Input
  
**Interrupts** are used to perform an action when the selected input is triggered, either on the **falling** or **rising** edge.  
The following function can be coded in the **ExtraInit-Function** (monsterrhinostep.ino). In this case the interrupt is activated after a reset.

```C++
g_Input1.SetRunFallingFunction(INPUT_RUN_MOTOR_STOP_1);
```
**Actions:**
These are the defined values for an action, beginning with **INPUT_RUN_**:  
  
- NONE  
- USERFUNCTION_START_*[UserFunctionNr]* (optional: + *[SubFunctionNr]*) 
- USERFUNCTION_STOP_*[UserFunctionNr]*  (optional: + *[SubFunctionNr]*)
- MOTOR_STOP_*[MOTOR_NR]*  
- MOTOR_EMERGENCYSTOP_*[MOTOR_NR]* 
    
**Note:** All combinations are possible when using a motor action.  
 
```C++
g_Input1.SetRunFallingFunction(INPUT_RUN_MOTOR_STOP_1);
//Stop motor 1 at falling edge on input 1

g_Input2.SetRunRisingFunction(INPUT_RUN_MOTOR_STOP_2_3_4);
//Stop motor 2,3 and 4 at rising edge on input 2

g_Input3.SetRunRisingFunction(INPUT_RUN_MOTOR_STOP_1_2_3_4);
//Stop motor 1,2,3 and 4 at rising edge on input 3

g_Input4.SetRunFallingFunction(INPUT_RUN_USERFUNCTION_1 + 2); 
//Start user function 1 sub 2 (parameter Par=2) at falling edge on input 4
```  
The **state** of an input can be read with these both functions ```g_Input1.GetStatus()``` or ```digitalRead(PIN_INPUT1)``` 
```C++
if(digitalRead(g_Input1)==1){
  Serial.print("Hello world");
}
```

### Input example
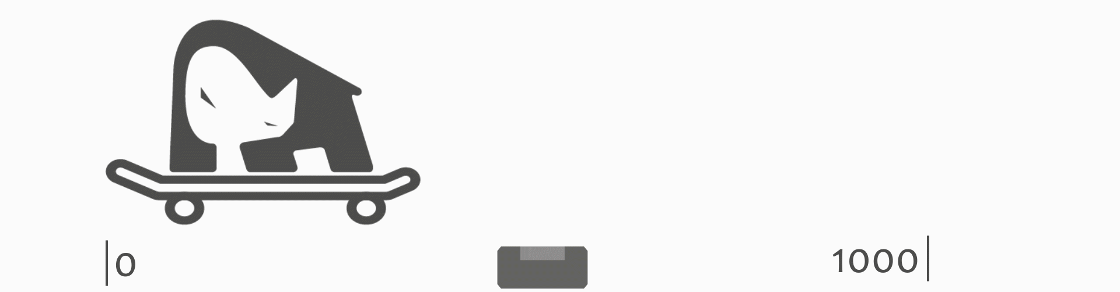
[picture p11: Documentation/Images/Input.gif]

```C++
//FILE "monsterrhinostep.ino":
void ExtraInit(){
  g_Input1.SetRunFallingFunction(INPUT_RUN_USERFUNCTION_1);
  //Set interrupt to input 1 with the event "Call UserFunction1"
  g_Motor1.SetTargetPosition(1000);
  return;
}

//FILE "User_Function1.cpp":
uint32_t UserFunction1(uint32_t par, UserFunction* pUserFunction)
  g_Motor1.SetTargetPosition(0);
  //Return to position zero when this function is called
  return 1;
}

```
**see also:** [Input commands]

## Analog output
Monsterrhino Motion features three analog (PWM) outputs. This outputs are either open-drain (floating value) or pulled to ground. With PWM-control you can decide the "analog"-Value of each output with the corresponding frequency.

Serial command:
```
s pf 100
//Set PWM frequency to 100 Hz
s pw1 120
//Set PWM-value (0-255) to 120
```
Code:
```C++
g_System.SetPWM(nr, value);
g_System.SetPWMFrequency( value);
```

## Digital output
One digital output (+24V DC, 1A) can be used on the MonsterrhinoMotion as follows.  
<!--TODO: how much Ampere ?-->

Serial command:
```
s o 0
//system_output_0: Set output OFF/LOW
s o 1
//system_output_1: Set output ON/HIGH
s o 2
//system_output_2: Toggle output state
s o ?
//system_output_?: Return output state
```
Code:
```C++
g_System.SetOutput(0);
//Set output OFF/LOW
g_System.SetOutput(1);
//Set output ON/HIGH
g_System.SetOutput(2);
//Toggle output state

int state = g_System.GetOutput();
//Return output state
```
## Encoder
Each motor channel features an encoder input.  
The resolution of an encoder can be set with the function ```g_Motor1.SetEncoderResolution(200, 4000);```. In this example our encoder has **200 motor steps** and **4000 cpr** (counts per revolution).  
The **Deviation flag** is triggered (if active), when the internal steps have a certain amount of difference to the encoder step count. This flag can activated  with this function ```g_Motor1.SetEncoderDeviation(10);```.

Serial command:
```
m1ep ?
//Return Encoder position
```
Code:
```C++
double EncValue = g_Motor1.GetEncoderPosition();

g_Motor1.IsEncoderDeviationDetected();
//returns true (bool) if a deviation is detected
g_Motor1.ClearEncoderDeviationFlag();
//if a deviation is detected the flag needs to be cleared manually
```

## Using other motors
Monsterrhino Motion can power many types of motors.  
The **onboard sense resistor** (220mOhms) can feature motors with a **RMS-current** of up to **1.1A**.  

To use **motors with higher current** the default sense resistor needs to be **unsoldered** and an other soldered on. In the following table you can see the sense resistor value with its corresponding current value.

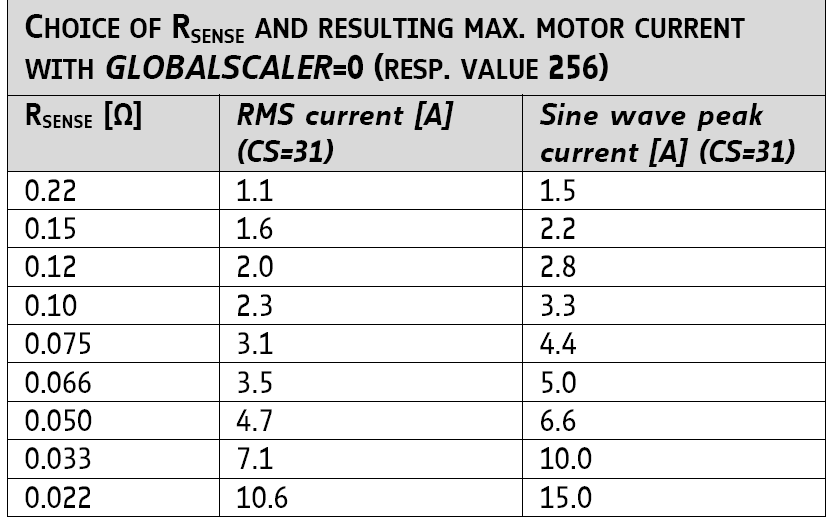
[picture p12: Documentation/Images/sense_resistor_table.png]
Sense resistor table


Before we start to work with the new motor, the sense resistor value needs to be changed via USB-commands or in the code as follows:  
(example on motor1 with sense resistor 75mOhms)

Serial command:
```
m1st sr 75
//motor1 startup sense resistor 75mOhms
s save
//system save to eeprom
s reset
//reboot system
```
Code:
```C++
g_Motor1.SetMotorSenseResistor(75);

```
## Events
Events provide the machine to react on different actions depending on motor status, user function status, input status and time.  

One or more trigger actions can be set as parameters in these function.  
They need to be **separated with a bar "|"**.

After defining the event condition you need to hold your task with ```pUserFunction->WaitEvent()```. This function holds the task until a selected action is triggered.  
**Trigger action** list: 

- MOTORIOEVENT_MOTOR1PosReached
- MOTORIOEVENT_MOTOR1StallGuard
- MOTORIOEVENT_MOTOR1StopLeft
- MOTORIOEVENT_MOTOR1StopRigth
- MOTORIOEVENT_INPUT1_FallingLow
- MOTORIOEVENT_INPUT1_RisingHigh
- USERFUNCTIONEVENT_EXIT

### SetOrCondition
This function waits until one (or one of multiple conditions is satisfied) condition is satisfied. 
```C++
g_Motor1.ResetRampStatus();

pUserFunction->m_MotorIoEvent.SetOrCondition(MOTORIOEVENT_MOTOR1PosReached);
if (pUserFunction->WaitEvent() == USERFUNCTIONEVENT_EXIT) return false;
```
of multple conditions: 
```C++
g_Motor1.ResetRampStatus();
g_Motor4.ResetRampStatus();

pUserFunction->m_MotorIoEvent.SetOrCondition(MOTORIOEVENT_MOTOR1PosReached | MOTORIOEVENT_MOTOR4PosReached);
if (pUserFunction->WaitEvent() == USERFUNCTIONEVENT_EXIT) return false;
```

The ```g_Motor2.ResetRampStatus();``` is necessary to clear the event status. 

### SetAndCondition
This function waits until all given conditions are satisified.
```C++
g_Motor3.ResetRampStatus();

pUserFunction->m_MotorIoEvent.SetAndCondition(MOTORIOEVENT_MOTOR3PosReached);
if (pUserFunction->WaitEvent() == USERFUNCTIONEVENT_EXIT) return false;
```
of multple conditions: 
 
```C++
g_Motor3.ResetRampStatus();
g_Motor4.ResetRampStatus();

pUserFunction->m_MotorIoEvent.SetAndCondition(MOTORIOEVENT_MOTOR3PosReached | MOTORIOEVENT_MOTOR4PosReached);
if (pUserFunction->WaitEvent() == USERFUNCTIONEVENT_EXIT) return false;
```

The ```g_Motor2.ResetRampStatus();``` is necessary to clear the event status.

### Event example

This example shows you how to use an event.  
Motor1 and Motor2 turn to a relative position and the task is finished when both motors have reached their position **and** input7 is triggered low.

```C++
g_Motor1.ResetRampStatus();
g_Motor2.ResetRampStatus();
g_Motor1.SetMoveRelative(500);
g_Motor2.SetMoveRelative(2000);

pUserFunction->m_MotorIoEvent.SetAndCondition(MOTORIOEVENT_MOTOR1PosReached |
	MOTORIOEVENT_MOTOR2PosReached | MOTORIOEVENT_INPUT7_FallingLow);
//Set "AND"-event
if (pUserFunction->WaitEvent() == USERFUNCTIONEVENT_EXIT) return false;
//wait until (motor1 position reached && motor2 position reached && input7 falling low)
Serial.println("continue task");
```
**Note:** The statement ```if (pUserFunction->WaitEvent() == USERFUNCTIONEVENT_EXIT) return false;``` activates the wait event, in addition it can leave the task when the serial command ```f1t``` (stop userFunction task) is received.

## Special functions  

Special functions are stall guard, coolStepping, power stage tuning and stealth chop.
*TODO*
<!-- 
TODO: Add this special functions
-->

## Emergency switch
This feature **cuts off the motor power supply**, by removing the EM-jumper on the Motion (see animation).  
It is possible to add an external NC-switch (EM-jumper removed, pins: 3v3,EM).  
After checking the emergency cause, you **should reset** your board. The Motion does not stop sending commands if an emergency event occurs, therefore **actions could be lost or people harmed !**



<!-- 
TODO: Code example read/Set
g_Motor[i].EmergencyStop(reset=true);
-->

**Note:** The pin /EM has an installed pull-down resistor and can only be supplied with 3.3V DC.

# CAN 
CAN is a commonly used communication system in automotive, automation and others.  
Due to its high reliability and higher speed than UART it can be used to communicate with the Motion from another Motion or, as an example, a RaspberryPi or Arduino (with a CAN-module).  

Up to 4 Monsterrhino boards can be connected via CAN to communicate with each other. It is also possible to connect other devices that support CAN communication.  

CAN functions can be used in user functions as following:  

```c++
pUserFunction->RemoteCommand_Motor_SetTargetPosition(3, 1, 200);
//Set target position of motor 1 on board with address 3 to value 200
//address: 3; motorNr:1; Value:200

pUserFunction->RemoteCommand_UserFunction_SetStart(2, 2, 1);
//Start user function 2 sub function 2 on board with address 2
//address: 2; functionNr:2; subFunction:1

uint32_t testVariable = 0;
pUserFunction->RemoteCommand_UserFunction_GetVariable(4, 1, 5, testVariable);
//Get user function variable 5 of user function 1 on board with address 4 and write to testVariable
//address: 5; functionNr:1; functionVar:5; testVariable: variable with return value
```
The remoteCommand function supports all serial command functions.  
In addition you can get and set **user function variables** via remoteCommand as shown above.

## Board setup for CAN  

Switch 1 (SW1, CAN TERM) activates CAN termination resistor (120 Ohm) (1 is active).  
Switch 2 (SW2, BOARD ID) indicates CAN address (BoardID+2) as follows:

SW2_1     |SW2_2    |Address|Board ID
-----|------|------|-----
LOW   |LOW  |   2  |0
HIGH  |LOW  |   3  |1
LOW   |HIGH |   4  |2
HIGH  |HIGH |   5  |3

The can adress can be checked with the serial command `s ca ?`  

**Note**:  
Address 0 is reserved for a broadcast message.  
Address 1 is reserved for other devices.  

## Variables
Each [User Function] has a total of **12 public variables** with two types (uint32, double) each 6.  
These variables have the ability to be read and/or be set over CAN communication.  
These variables can be used in CAN-communication.
```C++
pUserFunction->m_variable[0] = 0; //m_variable[0]=0 of current UserFunction
pUserFunction->m_variableFloat[4] = 3.45;
```
**Note:** *m_variable[6]* is **no** variable because each Userfunction offers six of each type.  
0-5 equals a total of 6.

## CAN bus communication protocol

### Compose a CAN message
Commands can also be send over the CAN bus, therefore it is necessary to set the correct bits in the CAN frame. We use the extended CAN frame with 29 bits with our own can protocol. 
The following paragraphs describe the use of the bits within our CAN frame.

### CAN frame overview
The can frame is composed of an **address part** and a **data field**. The 29 bits identifier of the extended CAN frame are split as follows

Addressing bit |Function   | Description
:-----|:------:|------:
0-3  |address number  |  (0-15) 
4-13  |sub command |   (9 bit = 512) 
14-17 |command |   (0-15) **see below** 				
 18  |error	| active low
19-23  | to Address | 0 = broadcast, 2-31 = to address **see below** 
24-28 |from Address | 0 = bus controller, 2-31 = from address **see below** 
29 |    identifies respond message    |0 = respond message, 1= send message

Data byte |Function   | Description
:-----|:------:|------:
Byte MSB-0  | return function ID | bit 0-7 (0-127)
Byte MSB-0  | get value | bit 7 = 1
MSB-1 - MSB-7 | data | length and type depending on the register

### Command

Value | Aberration | Function
:-----|:------:|------:
0 | (**s**)  | System
1  | (**m**)  | Motor
2  | (**i**)  | Input
3  | (**f**)  | User function

### Address range

Value |  Function
:-----|------:
0 |broadcast message
1| Bus controller
2-31| Available address range for clients

### Sub command of motor command

Value |  Function | Comment
:-----|:------:|------:
0|	emergency stop |no data
1 |stop | no data
2 | enable/disable driver | data type <byte>: 0:disabel driver, 1:enable driver
3 | RampMode | data type (uint8) <Set><Get> **0: Positioning mode** (using all A, D and V parameters) **1: Velocity** mode to positive VMAX (using AMAX acceleration) **2: Velocity** mode to negative VMAX (using AMAX acceleration) **3: Hold mode** (velocity remains unchanged,unless stop event occurs)
4 |	TargetPosition | (int48) <Set><Get>									the target position (step*1000) /!\ Set all other motion profile parameters before data type <double*1000>
5 |	TargetPosition Register | (int32) <Set><Get>							the target position (micro steps) /!\ Set all other motion profile parameters before data type <int32>
6|	MoveRelative |(int32) <Set>											Move motor relative (steps x 1000) data type <double x 1000>
7|	MoveRelative Register| (int32) <Set>									Move motor relative (micro steps) data type <int32>
8|	CurrentPosition | (int48) <Set><Get>					 				the current internal position (steps x 1000) data type <double x 1000>
9 |	CurrentPositionRegister| (int32) <Set><Get>					 		the current internal position (micro steps) data type <micro steps>
10 | Max Speed| (uint32) <Set>											the max speed VMAX data type <float*1000>
11|	Max Speed |Register (uint32) <Set><Get>								Register max speed VMAX	-data type <uint32>
12| Ramp speed Start |(uint32) <Set><Get>									the start ramp speed	-data type <float*1000>
13|	Ramp speed Start Register |(uint32) <Set><Get>						Register Ramp speed Start	-data type <uint32>
14| Ramp speed Stop | (uint32) <Set><Get>									the stop ramp speed	-data type <float*1000>
15|	Ramp speed Stop Register |(uint32) <Set><Get>						Register Ramp speed Stop	-data type <uint32>
16| Ramp speed Hold|(uint32) <Set><Get>									the hold ramp speed	-data type <float*1000>
17|	Ramp speed Hold Register |(uint32) <Set><Get>						Register Ramp speed Hold	-data type <uint32>
18|	get Current Speed|(uint32)	<Get>									Return the current speed	-data type <float*1000>
19|	get Current Speed Register |(uint32) <Get>							Return the current  speed Register 	-data type <uint32>
20| Acceleration AMAX|(uint32) <Set><Get>								 ramp accelerations AMAX	-data type <float*1000>
21|	 Acceleration AMAX Register|(uint32) <Set><Get>						Register  Acceleration AMAX	-data type <uint32>
22| Acceleration DMAX |(uint32) <Set><Get>								ramp accelerations DMAX		-data type <float*1000>
23|	 Acceleration DMAX Register|(uint32) <Set><Get>						Register  Acceleration DMAX	-data type <uint32>
24| Acceleration A1|(uint32) <Set><Get>									ramp accelerations A1	-data type <float*1000>
25|	 Acceleration A1 Register|(uint32) <Set><Get>						Register  Acceleration A1		-data type <uint32>
26| Acceleration D1|(uint32) <Set><Get>									ramp accelerations D1		-data type <float*1000>
27|	 Acceleration D1 Register|(uint32) <Set><Get>						Register  Acceleration D1	-data type <uint32>
28| ModeChangeSpeeds pwmThrs|(uint32) <Set><Get>							mode change speeds pwmThrs		-data type <float*1000>
28|	 ModeChangeSpeeds pwmThrs Register|(uint32) <Set><Get>				Register  ModeChangeSpeeds pwmThrs	-data type <uint32>
30| ModeChangeSpeeds coolThrs|(uint32) <Set><Get>						mode change speeds coolThrs		-data type <float*1000>
21|	 ModeChangeSpeeds coolThrs Register|(uint32) <Set><Get>				Register ModeChangeSpeeds coolThrs		-data type <uint32>
32| ModeChangeSpeeds highThrs|(uint32) <Set><Get>						mode change speeds highThrs -data type <float*1000>
33|	 ModeChangeSpeeds highThrs Register|(uint32) <Set><Get>				Register ModeChangeSpeeds highThrs			-data type <uint32>
34|	Encoder Position |(int48) <Set><Get>									the current encoder position (micro steps)	-data type <double*1000>
35|	Encoder Position Register|(uint32) <Set><Get>						the current encoder position (steps*1000)	-data type <uint32>
36|	Latched Position |(int48) <Set><Get>									the current latched position (micro steps)	-data type <double*1000>
37|	Latched Position Register|(uint32) <Set><Get>						the Latched position (steps*1000)		-data type <uint32>
38|	LatchedEncoderPosition |(int48) <Set><Get>							the current latched encoder position (steps x 1000)		-data type <double x 1000>
39|	LatchedEncoderPosition Register|(int32) <Set><Get>					the current latched encoder position (uSteps)		-data type <int32>|
50|	EncoderResolution_motorSteps |(int32) <Set><Get>						the number of steps per turn for the motor -data type <int32>
51|	EncoderResolution_encResolution |(int32) <Set><Get>					the actual encoder resolution (pulses per turn) -data type <int32>
53|	EncoderIndexConfiguration |(uint8 bit bit bit bit ) <Set>			Configure the encoder N event context. -data type <uint8>													**sensitivity** : set to one of ENCODER_N_NO_EDGE, ENCODER_N_RISING_EDGE, ENCODER_N_FALLING_EDGE, ENCODER_N_BOTH_EDGES -data type <bit>													**nActiveHigh** : choose N signal polarity (true for active high) -data type <bit>	**ignorePol** : if true, ignore A and B polarities to validate a N event -data type <bit>	**aActiveHigh** : choose A signal polarity (true for active high) to validate a N event -data type <bit> **bActiveHigh** : choose B signal polarity (true for active high) to validate a N event -data type <bit>
54|	EncoderLatching  |(uint8) <Set>										Enable/disable encoder and position latching on each encoder N event (on each revolution)-data type <uint8>
55|	isEncoderDeviationDetected|(uint8) <Get>								Check if a deviation between internal pos and encoder has been detected-data type <uint8>
56| clearEncoderDeviationFlag|() <Set>									Clear encoder deviation flag (deviation condition must be handled before) -no data
57| EncoderAllowedDeviation |(int32) <Set>								Encoder Allowed Deviation -data type <uint32>
58| SW_Mode |(uint16) <Set><Get>											Reference Switch & StallGuard2 Event Configuration Register; See the TMC 5160 datasheet page 43 -data type <uint16>
59| DRV STATUS|(uint32) <Get>											StallGuard2 Value and Driver Error Flags; datasheet page 56 -data type <uint32>
60| GetRampStatus|(uint16) <Get><Reset>									RAMP_STAT � Ramp & Reference Switch Status Register; datasheet page 44 -data type <uint16>
61| GetGstat|(uint8) <Get><Reset>										Global status flags -data type <uint
67| SenseResistor|(uint16) <Set><Get>									sense Resistor in mOhms 0=automatic -data type <uint16>
68| MotorCurrent|(uint16) <Set><Get>										Motor Current in mA -data type <uint16>
69| MotorCurrentReduction|(uint16) <Set><Get>							Motor current reduction in mA -data type <uint16>
70| Motor Freewheeling Mode|(uint8) <Set><Get>							Motor freewheeling mode -data type <uint8>**FREEWHEEL_NORMAL**   = 0x00, Normal operation **FREEWHEEL_ENABLED**  = 0x01, Freewheeling **FREEWHEEL_SHORT_LS** = 0x02, Coil shorted using LS drivers **FREEWHEEL_SHORT_HS** = 0x03 Coil shorted using HS drivers
71| Iholddelay|(uint8) <Set><Get> Controls the number of clock cycles for motor power down after a motion as soon as standstill is detected (stst=1) and TPOWERDOWN has expired.The smooth transition avoids a motor jerk upon power down. -data type <uint8> 0: instant power down 1-15: Delay per current reduction step in multiple	of 2^18 clocks
72| PWM_OFS| (uint8) <Set><Get> user defined PWM amplitude offset (0-255) related to full -data type <uint8> motor current (CS_ACTUAL=31) in stand still.(Reset default=30)
73| PWM_GRAD|(uint8) <Set><Get>	 Velocity dependent gradient for PWM amplitude: PWM_GRAD * 256 / TSTEP This value is added to PWM_AMPL to compensate for	the velocity-dependent motor back-EMF. -data type <uint8>
74| StepperDirection|(uint8) <Set><Get>									Velocity motor  Stepper Direction -data type <uint
75| UnLook Motor|(uint8) <Set><Get>										Unlock Motor -data type <uint8>	This value is added to PWM_AMPL to compensate for	the velocity-dependent motor back-EM
90| Homing Mode|(uint8) <Set/Start><Get>									Start homing -data type <uint8> 1: endswitsh left; 2: endswitsh right
91| Homing timeOut |(uint32) <Set><Get>									homing time to fail -data type <uint32>
92| Homing maxPos| (uint32) <Set><Get>									maximal deviation Posipion to fail -data type <uint32>
93| Homing rampSpeed |(uint32) <Set><Get>								rampSpeed for the homing process -data type <float*1000>
94| Homing rampSpeed Register |(uint32) <Set><Get>						Register rampSpeed for the homing process -data type <uint32>
95| Homing rampSpeed_2|(uint32) <Set><Get>								rampSpeed phase 2 -data type <float*1000>
96| Homing rampSpeed_2 Register| (uint32) <Set><Get>						Register rampSpeed_2 for the homing process phase 2 -data type <uint32>
97| Homing Offset|(uint48) <Set><Get>									homing offset(microstep) -data type <float*1000>
98| Homing Offset Register| (uint32) <Set><Get>							Register homing offset(microstep) -data type <uint32>
99| Homing rampSpeedStart|(uint32) <Set><Get>							homing ramp speed start -data type <double*1000>
100| Homing rampSpeedStart Register |(uint32) <Set><Get>					Register rampSpeedStart() -data type <uint32>
101| Homing rampSpeedStop|(uint32) <Set><Get>							homing ramp speed stop -data type <float*1000>
102| Homing rampSpeedStop Register| (uint32) <Set><Get>					Register rampSpeedStop() -data type <uint32>
103| Homing rampSpeedHold|(uint32) <Set><Get>							homing ramp speed hold -data type <float*1000>
104| Homing rampSpeedHold Register| (uint32) <Set><Get>					Register rampSpeedHold() -data type <uint32>
105| Homing accelerationsAmax|(uint32) <Set><Get>						homing accelerations Amax -data type <float*1000>
106| Homing accelerationsAmax Register| (uint32) <Set><Get>				Register accelerationsAmax() -data type <uint32>
107| Homing accelerationsDmax|(uint32) <Set><Get>			 			homing accelerations Dmax -data type <float*1000>
108| Homing accelerationsDmax Register |(uint32) <Set><Get>				Register accelerationsDmax() -data type <uint32>
109 |Homing accelerationsA1|(uint32) <Set><Get>							homing accelerations A1 -data type <float*1000>
110| Homing accelerationsA1 Register| (uint32) <Set><Get>				Register accelerationsA1() -data type <uint32>
111|Homing accelerationsD1|(uint32) <Set><Get>			 				homing accelerations D1 -data type <float*1000>
112| Homing accelerationsD1 Register| (uint32) <Set><Get>				Register accelerationsD1() -data type <uint32>
128|Startup  drvStrength|(uint32) <Set><Get>			 					Startup Selection of gate driver current. Adapts the gate driver current to the gate charge of the external MOSFETs.-data type <uint8> 00: weak 01: weak+TC (medium above OTPW level) 10: medium 11: strong
129|Startup  bbmClks|(uint32) <Set><Get>			 						Startup 0..15: Digital BBM time in clock cycles (typ. 83ns).The longer setting rules (BBMTIME vs. BBMCLKS). -data type <uint16> (Reset Default: OTP 4 or 2)
130|Startup  bbmTime|(uint32) <Set><Get>			 						Startup Break-Before make delay -data type <uint8> 0=shortest (100ns), 16 (200ns), 24=longest (375ns) ,>24 not recommended, use BBMCLKS instead
131|Startup  Iholddelay|(uint8) <Set><Get>								Startup	Iholddelay -data type <uint8>
132|Startup  SenseResistor|(uint16) <Set><Get>							Startup sense resistor in mOhms 0=automatic -data type <uint16> 
133|Startup  MotorCurrent|(uint16) <Set><Get>							Startup motor current in mA -data type <uint16>
134|Startup  MotorCurrentReduction|(uint16) <Set><Get>					Startup motor current reduction in mA -data type <uint16>
135|Startup  Motor Freewheeling Mode|(uint8) <Set><Get>					Startup motor freewheeling mode -data type <uint8>
136|Startup  PWM_OFS|(uint8) <Set><Get>									Startup	user defined PWM amplitude offset (0-255) related to full -data type <uint8>
137|Startup  PWM_GRAD|(uint8) <Set><Get>									Startup	Velocity dependent gradient for PWM amplitude: PWM_GRAD * 256 / TSTEP -data type <uint8>
138|Startup  StepperDirection|(uint8) <Set><Get>							Startup	Velocity motor  Stepper Directio -data type <uint8>
139|Startup  MaxSpeed |(uint32) <Set><Get>								Startup	the max speed VMAX -data type <float*1000>
140|Startup  MaxSpeed Register |(uint32) <Set><Get>						Register Startup  MaxSpeed -data type <uint32>
141|Startup  StartRampSpeed|(uint32) <Set><Get>							Startup	the start ramp speed -data type <float*1000>
142|Startup  StartRampSpeed Registerv (uint32) <Set><Get>				Register Startup  start ramp speed -data type <uint32>
143|Startup  StopRampSpeed|(uint32) <Set><Get>							Startup	the stop ramp speed -data type <float*1000>
144|Startup  StopRampSpeed Register |(uint32) <Set><Get>					Register Startup  stop ramp speed -data type <uint32>
145|Startup  HoldRampSpeed|(uint32) <Set><Get>							Startup	the hold ramp speed -data type <float*1000>
146|Startup  HoldRampSpeed Register |(uint32) <Set><Get>					Register Startup  hold ramp speed -data type <uint32>
147|Startup  Acceleration maxAccel|(uint32) <Set><Get>					Startup	ramp accelerations AMAX -data type <float*1000>
148|Startup  Acceleration maxAccel Register |(uint32) <Set><Get>			Register Startup  Acceleration maxAccel -data type <uint32>
149|Startup  Acceleration maxDecel|(uint32) <Set><Get>					Startup	ramp accelerations DMAX -data type <float*1000>
150|Startup  Acceleration maxDecel Register| (uint32) <Set><Get>			Register Startup  Acceleration maxDecel -data type <uint32>
151|Startup  Acceleration startAccel|(uint32) <Set><Get>					Startup	ramp accelerations A1 -data type <uifloat*1000nt32>
152|Startup  Acceleration startAccel Register |(uint32) <Set><Get>		Register Startup  Acceleration startAccel -data type <uint32>
153|Startup  Acceleration stopAccel|(uint32) <Set><Get>					Startup	ramp accelerations D1 -data type <float*1000>
154|Startup  Acceleration stopAccel Register|(uint32) <Set><Get>		Register Startup  Acceleration stopAccel -data type <uint32>
155|Startup  ModeChangeSpeeds pwmThrs|(uint32) <Set><Get>				Startup	mode change speeds pwmThrs -data type <float*1000>
156|Startup  ModeChangeSpeeds pwmThrs Register| (uint32) <Set><Get>		Register Startup  ModeChangeSpeeds pwmThrs -data type <uint32>
157|Startup  ModeChangeSpeeds coolThrs|(uint32) <Set><Get>				Startup	mode change speeds coolThrs -data type <float*1000>
158|Startup  ModeChangeSpeeds coolThrs Register v(uint32) <Set><Get>		Register Startup  ModeChangeSpeeds coolThrs -data type <uint32>
159|Startup  ModeChangeSpeeds highThrs|(uint32) <Set><Get>				Startup	mode change speeds highThrs -data type <float*1000>
160|Startup  ModeChangeSpeeds highThrs Register |(uint32) <Set><Get>		Register Startup  ModeChangeSpeeds highThrs -data type <uint32>
161|Startup  EncoderResolution_motorSteps| (int32) <Set><Get>		Startup	the number of steps per turn for the motor -data type <int32>
162|Startup  EncoderResolution_encResolution| (int32) <Set><Get>		Startup	the actual encoder resolution (pulses per turn) -data type <int32>
164|Startup  EncoderIndexConfiguration| (uint8 bit bit bit bit ) <Set><Get>		Startup	Configure the encoder N event context. -data type <uint8>													**sensitivity** : set to one of ENCODER_N_NO_EDGE, ENCODER_N_RISING_EDGE, ENCODER_N_FALLING_EDGE, ENCODER_N_BOTH_EDGES -data type <bit> **nActiveHigh** : choose N signal polarity (true for active high) -data type <bit> **ignorePol** : if true, ignore A and B polarities to validate a N event -data type <bit> **aActiveHigh** : choose A signal polarity (true for active high) to validate a N event -data type <bit> **bActiveHigh** : choose B signal polarity (true for active high) to validate a N event -data type <bit> **Startup	Enable/disable encoder** and position latching on each encoder N event (on each revolution)
166;|Startup  EncoderAllowedDeviation |(int32) <Set><Get>				Startup	Encoder Allowed Deviation -data type <uint32>
167|Startup  SW_Mode |(uint16) <Set><Get>							Startup	Reference Switch & StallGuard2 Event Configuration Register; See the TMC 5160 datasheet page 43 -data type <uint16>
168|Startup  RampMode |(uint8) <Set><Get>							Startup	 RampMode -data type <uint8> 0: **Positioning mode** (using all A, D and V parameters) 1: **Velocity mode to positive VMAX** (using AMAX acceleration) 2: **Velocity mode to negative VMAX** (using AMAX acceleration) 3: **Hold mode** (velocity remains unchanged,unless stop event occurs) "HomingMode","HomingOffset","HomingMaxPos","HomingTimeout","HomingSpeed_2","HomingDmax"
169|Startup  Homing Mode|(uint8) <Set><Get>							Startup	homing mode-data type <uint8>
170|Startup  Homing Offset|(int48) <Set><Get>						Startup	homing offset(microstep) -data type <double*1000>
171|Startup  Homing Offset Register |(int32) <Set><Get>				Register Startup	homing offset(microstep) -data type <int32>
172|Startup  Homing timeOut |(uint32) <Set><Get>						Startup	homing time to fail -data type <uint32>
173|Startup  Homing maxPos |(int32) <Set><Get>						Startup	homing maximal deviation Posipion to fail -data type <int32>
174|Startup  Homing rampSpeed_2|(uint32) <Set><Get>					Startup	homing rampSpeed phase 2 -data type <float*1000>
175|Startup  Homing rampSpeed_2 Register| (int32) <Set><Get>			Register homing Startup	rampSpeed_2 -data type <int32>
176|Startup  Homing accelerationsDmax|(uint32) <Set><Get>			Startup	homing accelerations Dmax -data type <float*1000>
177|Startup  Homing accelerationsDmax Register |(int32) <Set><Get>	Register homing Startup	accelerationsDmax -data type <int32>512	..768 Maping Motor Register -data type <int32/uint32>

### Subcommand of userfunction 

Value |  Function | Comment
:-----|:------:|------:
1| start user function|(uint8)  <Set><Get> Start userFunction whith sub user function data -data type <uint8>
2| stop user function|
30| userFunctionVariable1|(uint32)  <Set><Get>						Set/Get userFunction variable 1
31| userFunctionVariable2|(uint32)  <Set><Get>						Set/Get userFunction variable 2
32| userFunctionVariable3|(uint32)  <Set><Get>						Set/Get userFunction variable 3
33| userFunctionVariable4|(uint32)  <Set><Get>						Set/Get userFunction variable 4
34| userFunctionVariable5|(uint32)  <Set><Get>						Set/Get userFunction variable 5
35| userFunctionVariable6|(uint32)  <Set><Get>						Set/Get userFunction variable 6
40| userFunction Variable1 float|(uint48)(uint48/1000= double )  <Set><Get>					Set/Get userFunction float variable 1
41| userFunction Variable2 float|(uint48)(uint48/1000= double )  <Set><Get>					Set/Get userFunction float variable 2
42| userFunction Variable3 float|(uint48)(uint48/1000= double )  <Set><Get>					Set/Get userFunction float variable 3
43| userFunction Variable4 float|(uint48)(uint48/1000= double )  <Set><Get>					Set/Get userFunction float variable 4
50| Startup  start user function|(uint8)  <Set><Get>					Startup userFunction whith sub user function data
60| Startup userFunction Variable1|(uint32)  <Set><Get>				Startup Set/Get userFunction variable 1
61| Startup userFunction Variable2|(uint32)  <Set><Get>				Startup Set/Get userFunction variable 2
62| Startup userFunction Variable3|(uint32)  <Set><Get>				Startup	Set/Get userFunction variable 3
63| Startup userFunction Variable4|(uint32)  <Set><Get>				Startup	Set/Get userFunction variable 4
64| Startup userFunction Variable5|(uint32)  <Set><Get>				Startup	Set/Get userFunction variable 5
65| Startup userFunction Variable6|(uint32)  <Set><Get>				Startup	Set/Get userFunction variable 6
70| Startup userFunction Variable1 |float(uint48)(uint48/1000= double )  <Set><Get>			Startup	Set/Get userFunction float variable 1
71| Startup userFunction Variable2 |float(uint48)(uint48/1000= double )  <Set><Get>			Startup	Set/Get userFunction float variable 2
72| Startup userFunction Variable3 |float(uint48)(uint48/1000= double )  <Set><Get>			Startup	Set/Get userFunction float variable 3
73| Startup userFunction Variable4 |float(uint48)(uint48/1000= double )  <Set><Get>			Startup	Set/Get userFunction float variable 4

### Subcommand of input				
Value |  Function | Comment
:-----|:------:|------:
1 |inputFaling|(uint32)	<Set><Get> Input Faling INPUT_RUN_USERFUNCTION -data type <uint32>
2 |inputRising|(uint32)	<Set><Get> Input Rising INPUT_RUN_USERFUNCTION -data type <uint32>
3| Startup inputFaling|(uint32)	<Set><Get> Startup Input Faling INPUT_RUN_USERFUNCTION -data type <uint32>
4 |Startup inputRising|(uint32)	<Set><Get> Startup Input Rising INPUT_RUN_USERFUNCTION -data type <uint32>
5| GetInputState |<uint8><Get> Get the state of input -data type <uin32> descipion of 

Function |  Value | Comment
:-----|:------:|------:
INPUT_RUN_USERFUNCTION| | all fuctions can combinate 
INPUT_RUN_USERFUNCTION_START_1 | 0x0001xx	| Start userfunction 1 whit sub function xx
INPUT_RUN_USERFUNCTION_START_2 |0x000200	| Start userfunction 2 whit sub function xx
INPUT_RUN_USERFUNCTION_START_3 |0x000400	| Start userfunction 3 whit sub function xx
INPUT_RUN_USERFUNCTION_START_4 |0x000800	| Start userfunction 4 whit sub function xx
INPUT_RUN_USERFUNCTION_START_5 |0x001000	| Start userfunction 4 whit sub function xx
INPUT_RUN_USERFUNCTION_START_6 |0x002000	| Start userfunction 4 whit sub function
INPUT_RUN_USERFUNCTION_STOP_1 |0x010100	| Stop userfunction 1
INPUT_RUN_USERFUNCTION_STOP_2 |0x010200	| Stop userfunction 2
INPUT_RUN_USERFUNCTION_STOP_3 |0x010400	| Stop userfunction 3
INPUT_RUN_USERFUNCTION_STOP_4 |0x010800	| Stop userfunction 4
INPUT_RUN_USERFUNCTION_STOP_5| 0x011000	| Stop userfunction 5
INPUT_RUN_USERFUNCTION_STOP_6 |0x012000	| Stop userfunctio
INPUT_RUN_MOTOR_STOP_1 |0x020100	| Motor Stop 1
INPUT_RUN_MOTOR_STOP_2| 0x020200	| Motor Stop 2
INPUT_RUN_MOTOR_STOP_3 |0x020200	| Motor Stop 3
INPUT_RUN_MOTOR_STOP_4 |0x020400	| Motor Stop 4
INPUT_RUN_MOTOR_EMERGENCYSTOP_1 |0x022100	| EMERGENCYSTOP Motor  1
INPUT_RUN_MOTOR_EMERGENCYSTOP_2 |0x022200	| EMERGENCYSTOP Motor  1
INPUT_RUN_MOTOR_EMERGENCYSTOP_3 |0x022400	| EMERGENCYSTOP Motor  1
INPUT_RUN_MOTOR_EMERGENCYSTOP_4 |0x022800	| EMERGENCYSTOP Motor  1

# FAQ - Problems
## USB problems
**I can not connect to my MonsterrhinoMotion - I can not upload a program to my MonsterrhinoMotion - what can I do?**

* Sometimes there are problems with the USB connection or the COM port. To solve this it might help to use a USB hub or unplug the USB cable from the PC and plug to another USB port of the PC.
* If connecting to another port does not help you can try to disconnect all motors from the card. In most cases you can than upload the code correctly (DFU mode).
* Grounding metal plates where motors are mounted could also work.

**I get an error "target device not found". What should I do?**

* Sometimes when attempting to upload code to the MonsterrhinoMotion you get an error "target device not found", than it might be necessary to disconnect the motors from the card, disconnect and reconnect power from the card and then to try again to upload a program.

## Settings problems
**My motor settings are very strange and I am not able to change them. How can I reset the card?**

* In such a case open the **STMCubeProgrammer** connect via DFU mode to your MonsterrhinoMotion. After succefully connecting erase the card memory with the erasing button in the lower left corner. Now you can upload again from Arduino - now all parameters should be default values. 

## Motor problems
**My motor stands still, what can i do?**  

* Check the motor current and test with more or less current. For example, a motor with 100mA current could throw an error when set to 1000mA motor current (short to supply).  
When sending ```m1mds ?``` and the Flag "s2va" or "s2vb" is active the current value could be incorrect.
* Try to put ```g_Motor1.ResetRampStatus();``` before any motor action. Maybe a flag isnt cleared.

**My motor turns repeatedly 50 steps when homing**

* Your homing home is the wrong way so the motor starts in step 2 of homing. Try to change the homing parameter mode to 1 or 2.  

**Motor makes strange noise after uploading**

* This issue is probably caused by the motor controller, we havent solved this problem but normally resetting the board solves this problem

## CAN problems
**I can not send data to or from my board with CAN**  

* Check the CanSpeed ```s cs ?``` and board can adress ```s ca ?``` of all connected devices.  
* Check if the protocol is correct.  
* Check if something is sent. Just send continously data over the can bus and control the CAN-led on the motion board, if they dont blink maybe there is no data on the bus.

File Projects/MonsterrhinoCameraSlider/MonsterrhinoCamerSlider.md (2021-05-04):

# MonsterrhinoCameraSlider

## Setup

#### Assemble the car as seen on the images:
  
  * Connect the MonsterrhinoMotion and MonsterrhinoControl to the 24V source (e.g. battery). Foresee a power switch at the 24V line. 
  * Connect the CAN between MonsterrhinoMotion and MonsterrhinoControl
  * Connect the display to the MonsterrhinoControl
  * Connect the limit switches to the inputs of motor 2 on the MonsterrhinoMotion
  * Connect the motors: motor 1 linear sled, motor 2 camera rotation table, motor 4 object rotation table

#### Setup the Raspberry Pi 4

* Download a pre-installed Raspberry Pi image with the already installed CAN and display driver as described here: https://github.com/Monsterrhino/MonsterrhinoControl 
* Download the Python3 GUI software (https://github.com/Monsterrhino/MonsterrhinoMotion/tree/master/Projects/MonsterrhinoCameraSlider/python3) to the Raspberry Pi. You need to install some extra Python packages:

```Python
sudo pip3 install pillow
sudo apt-get install python3-pil python3-pil.imagetk
sudo apt-get install python3-opencv
sudo apt-get install libhdf5-dev
sudo apt-get install libhdf5-serial-dev
sudo apt-get install libatlas-base-dev
sudo apt-get install libjasper-dev 
sudo apt-get install libqtgui4 
sudo apt-get install libqt4-test
sudo pip3 install numpy

```

Now you should be able to run the software by executing following command in a terminal:

```Python
sudo python3 camera_slider.py
```

#### Setup the MonsterrhinoMotion

* Open the **Monsterrhinostep-Lib** through your ArduinoIDE (File->Examples->Monsterrhinostep->monsterrhinostep) and copy the content of the three files in https://github.com/Monsterrhino/MonsterrhinoMotion/tree/master/Projects/MonsterrhinoCameraSlider/firmware to the according files of the Monsterrhinostep-Lib (**monsterrhinostep, User_Function1 and User_Function2**).

* Compile and upload to your MonsterrhinoControl (further information of how to do that can be found in the docs) - and thats it!

#### **Attention:** Adjust settings

If the one motor spinns in the wrong direction you can use the USB commands within a serial monitor to fix that. To do so connect via serial monitor to your MonsterrhinoMotion card and type ``` m1st ?``` (change the number acording to the motor you need). You will see following output:

```C++
Get Startup: 
  drvStrength(drs): 0
  bbmTime(bt): 8
  bbmClks(bc): 0
  SenseResistor(sr): 220
  MotorCurrent(mA): 20
  MotorCurrentReduction(mAr): 20
  Freewheeling(fwm): 0
  Iholddelay(ihd): 7
  PwmOfsInitial(poi): 150
  PwmGradInitial(pgi): 30
  StepperDirection(sd): 0
  MotorSteps(mst): 200
  PWMThrs(pt): 0.00
  COOLThrs(ct): 0.00
  HighThrs(ht): 0.00
  SWMode(swm): 0
  RampMode(rm): 0
  RampMaxSpeed(ms): 200.00
  RampSpeedsStart(rms): 0.00
  RampSpeedsStop(rmt): 0.10
  RampSpeedsHold(rmh): 100.00
  AccelerationsAMax(AMax): 250.00
  AccelerationsDMax(DMax): 350.00
  AccelerationsA1(A1): 500.00
  AccelerationsD1(D1): 700.00
  CoolConf(CC): 0
  EncoderResolution(er): 0
  EncoderAlloweddeviation(ead): 0
  EncoderSetup(es): 0
  EncoderInverted(ei): 0
  HomingMode(hm): 0
  HomingOffset(ho): 0.00
  HomingMaxPos(hp): 1000000
  HomingTimeout(ht): 100000
  HomingSpeed_2(hs2): 10.00
  HomingDmax(hd): 2100.00
```
Now you can change the parameter **StepperDirection(sd): 0 ** to the opposite direction by entering ``` m1st sd 1``` into the terminal. Save the changes by typing ``` m1smp```.

It might also be necessary to change the motor currents, depending on the motors and mechanics you use. You can do so by changing the values of this lines (e.g. motor 4):

```C++
		g_Motor4.SetMotorCurrent(100);
		g_Motor4.SetMotorCurrentHold(10);
```

**Have fun!**

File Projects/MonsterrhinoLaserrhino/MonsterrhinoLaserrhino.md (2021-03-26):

# MonsterrhinoPrinterCar

## Setup

#### Assemble the car as seen on the images:
  
  * Connect the MonsterrhinoMotion and MonsterrhinoControl to the 24V source (e.g. battery). Foresee a power switch at the 24V line. 
  * Connect the CAN between MonsterrhinoMotion and MonsterrhinoControl
  * Connect the display to the MonsterrhinoControl
  * Connect the limit switches to the inputs of motor 3 and 4 on the MonsterrhinoMotion
  * Connect the 4 Monsterrhino RGB LEDs to the MonsterrhinoControl
  * Connect the motors: motor 1 and motor 2 are the front wheels, motor 3 is the z axis, and motor 4 is the y axis

  <br><br>
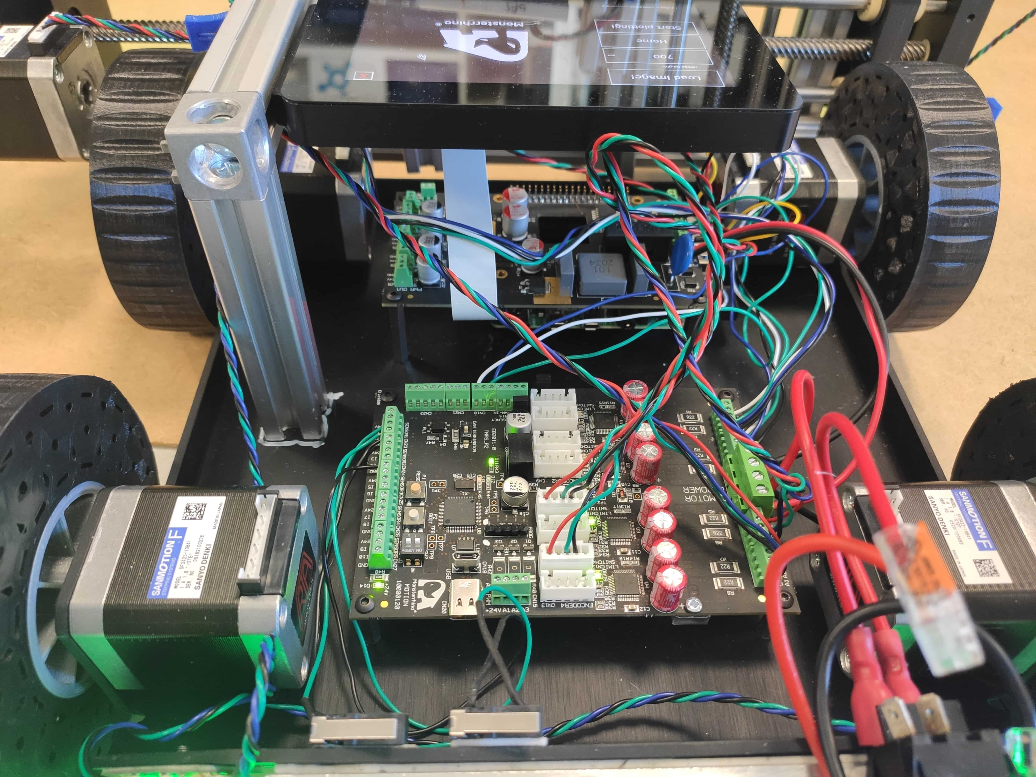
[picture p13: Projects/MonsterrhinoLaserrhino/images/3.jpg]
  
  <br><br>

#### Setup the Raspberry Pi 4

* Download a pre-installed Raspberry Pi image with the already installed CAN and display driver as described here: https://github.com/Monsterrhino/MonsterrhinoControl 
* Download the Python3 GUI software (https://github.com/Monsterrhino/MonsterrhinoMotion/Projects/MonsterrhinoPrinterCar/python3) to the Raspberry Pi. You need to install some extra Python packages:

```Python
sudo python3 led.py 
sudo pip3 install pillow
sudo apt-get install python3-pil python3-pil.imagetk
sudo apt-get install python3-opencv
sudo apt-get install libhdf5-dev
sudo apt-get install libhdf5-serial-dev
sudo apt-get install libatlas-base-dev
sudo apt-get install libjasper-dev 
sudo apt-get install libqtgui4 
sudo apt-get install libqt4-test
sudo pip3 install numpy

```

Now you should be able to run the software by executing following command in a terminal:

```Python
sudo python3 MonsterrhinoPrinterCarGUI.py
```

#### Setup the MonsterrhinoMotion

* Open the **Monsterrhinostep-Lib** through your ArduinoIDE (File->Examples->Monsterrhinostep->monsterrhinostep) and copy the content of the three files in https://github.com/Monsterrhino/MonsterrhinoMotion/Projects/MonsterrhinoPrinterCar/firmaware to the according files of the Monsterrhinostep-Lib (**monsterrhinostep, User_Function1 and User_Function2**).

* Compile and upload to your MonsterrhinoControl (further information of how to do that can be found in the docs) - and thats it!

#### Print
Place the .jpg file you whant to print on the Raspberry Pi, from the GUI select **Load Image!** and search for the path to the image file. After selecting the image you should see a preview of it on the screen. Tab home for homing the y-z axis. After homing has finished press **Start plotting**.

#### **Attention:** Adjust settings
If you have a different length of the rails, different tires, the motor mounted differently or a different gear ratio on the axis you have to adjust some parameters:

Change the following lines in User_Function1 in the function **Homing3and4** to adjust the range of your y and z axis: 

```C++
	// y axis
	g_Motor4.SetMoveRelative(-1550);  // this is the maximum that the y axis can move in steps

	// x axis
	g_Motor3.SetMoveRelative(-850);   // this is the maximum that the z axis can move in steps
```

If the one motor spinns in the wrong direction you can use the USB commands within a serial monitor to fix that. To do so connect via serial monitor to your MonsterrhinoMotion card and type ``` m1st ?``` (change the number acording to the motor you need). You will see following output:

```C++
Get Startup: 
  drvStrength(drs): 0
  bbmTime(bt): 8
  bbmClks(bc): 0
  SenseResistor(sr): 220
  MotorCurrent(mA): 20
  MotorCurrentReduction(mAr): 20
  Freewheeling(fwm): 0
  Iholddelay(ihd): 7
  PwmOfsInitial(poi): 150
  PwmGradInitial(pgi): 30
  StepperDirection(sd): 0
  MotorSteps(mst): 200
  PWMThrs(pt): 0.00
  COOLThrs(ct): 0.00
  HighThrs(ht): 0.00
  SWMode(swm): 0
  RampMode(rm): 0
  RampMaxSpeed(ms): 200.00
  RampSpeedsStart(rms): 0.00
  RampSpeedsStop(rmt): 0.10
  RampSpeedsHold(rmh): 100.00
  AccelerationsAMax(AMax): 250.00
  AccelerationsDMax(DMax): 350.00
  AccelerationsA1(A1): 500.00
  AccelerationsD1(D1): 700.00
  CoolConf(CC): 0
  EncoderResolution(er): 0
  EncoderAlloweddeviation(ead): 0
  EncoderSetup(es): 0
  EncoderInverted(ei): 0
  HomingMode(hm): 0
  HomingOffset(ho): 0.00
  HomingMaxPos(hp): 1000000
  HomingTimeout(ht): 100000
  HomingSpeed_2(hs2): 10.00
  HomingDmax(hd): 2100.00
```
Now you can change the parameter **StepperDirection(sd): 0 ** to the opposite direction by entering ``` m1st sd 1``` into the terminal. Save the changes by typing ``` m1smp```.

It might also be necessary to change the motor currents, depending on the motors and mechanics you use. You can do so by changing the values of this lines (e.g. motor 4):

```C++
		g_Motor4.SetMotorCurrent(100);
		g_Motor4.SetMotorCurrentHold(10);
```

**Have fun!**
  <br><br>
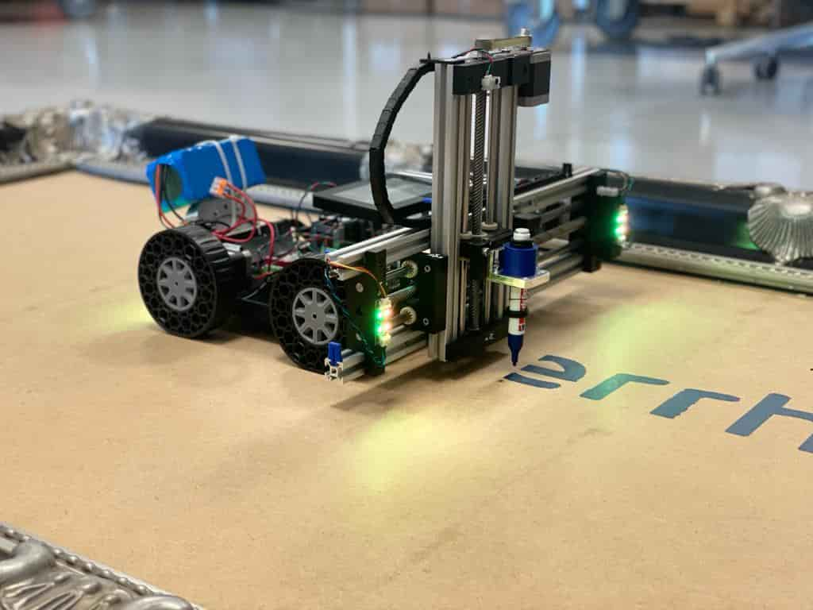
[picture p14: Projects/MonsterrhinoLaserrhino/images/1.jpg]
  
  <br><br>

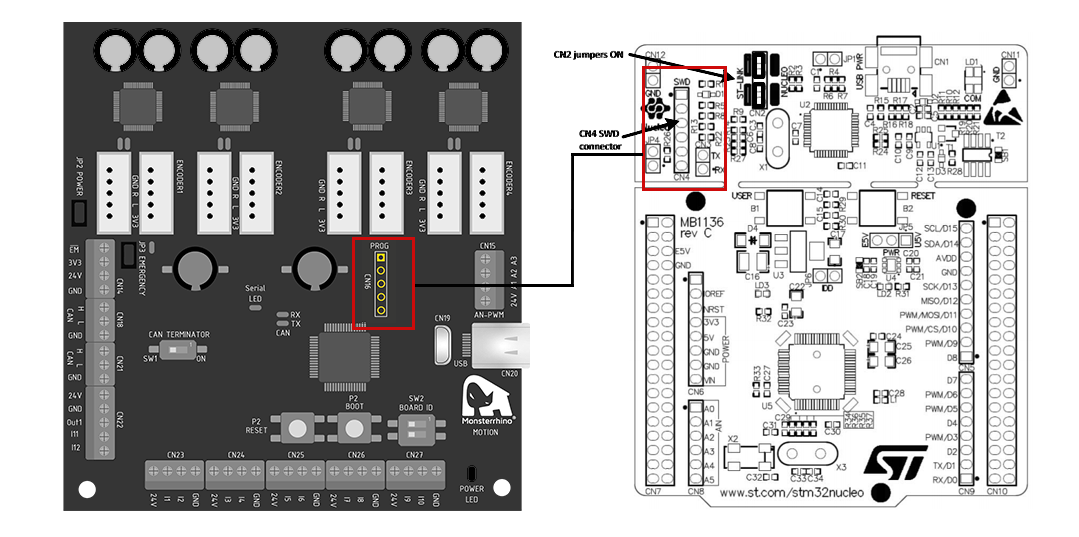
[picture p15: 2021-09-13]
Documentation/Images/NucleoPinout.png

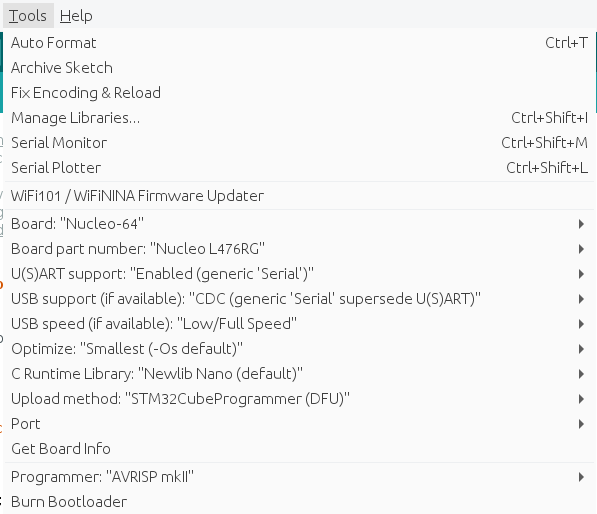
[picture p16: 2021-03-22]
Documentation/Images/settings.png

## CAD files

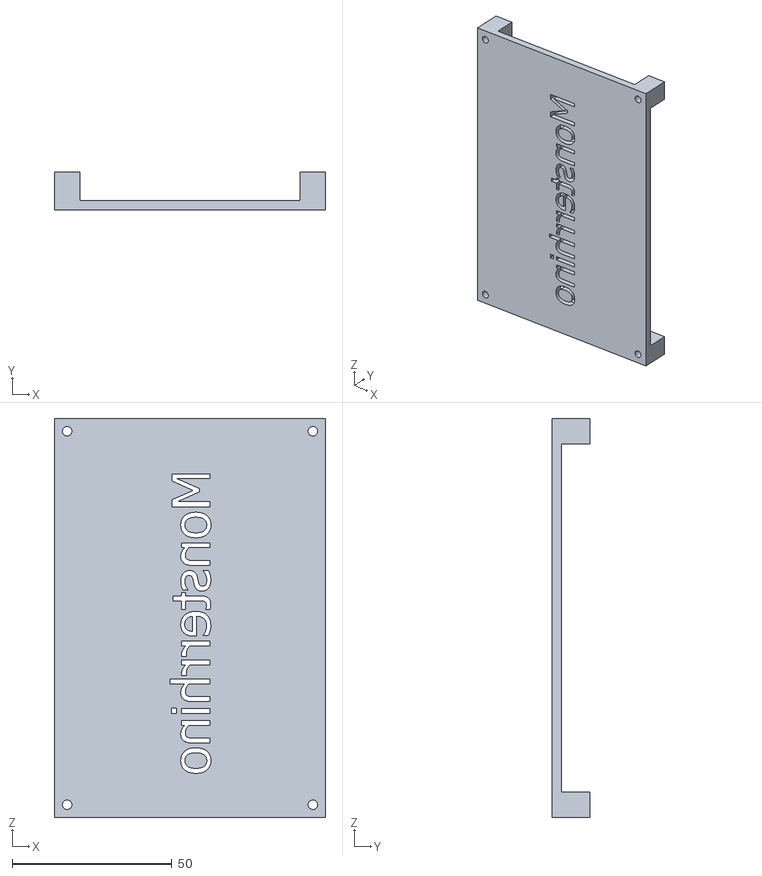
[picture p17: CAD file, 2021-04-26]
3d_files/monsterrhino_bottom_cover.stl
85.0 x 12.0 x 125.0

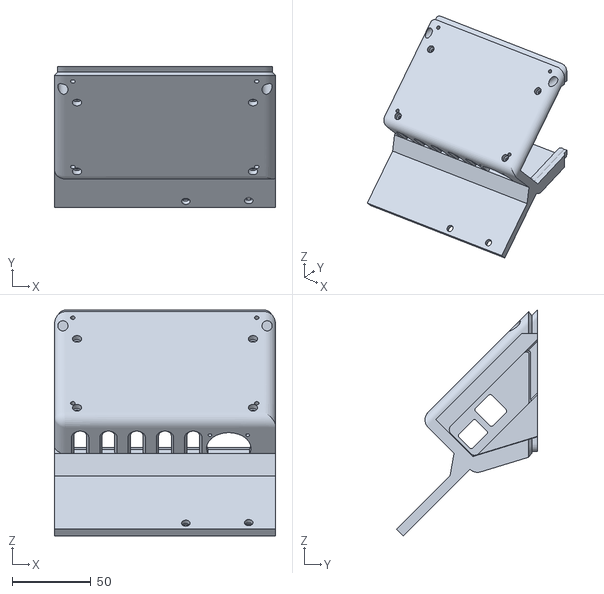
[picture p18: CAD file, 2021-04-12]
Projects/MonsterrhinoCameraSlider/3d_files/housing.stl
140.7 x 89.6 x 143.8

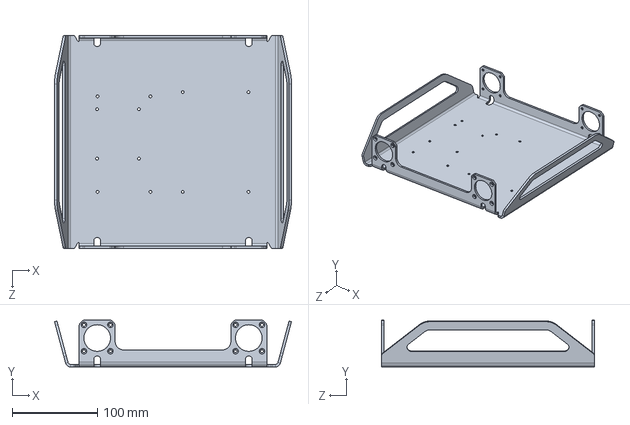
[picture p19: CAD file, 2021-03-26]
Projects/MonsterrhinoPrinterCar/3d_files/Chassis.STEP
278.1 x 55.0 x 250.0 mm

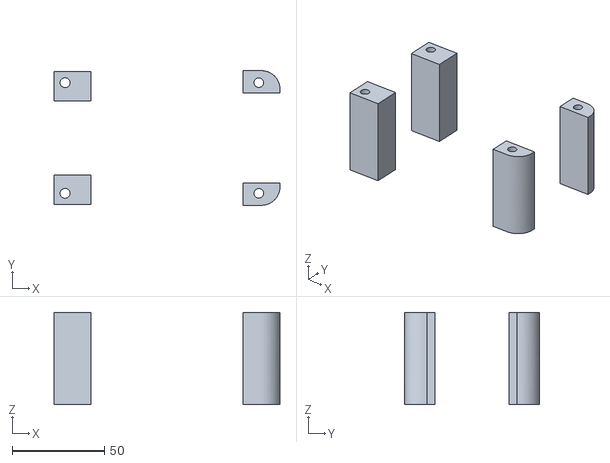
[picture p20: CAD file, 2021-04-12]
Projects/MonsterrhinoCameraSlider/3d_files/legs.stl
122.5 x 73.0 x 50.0

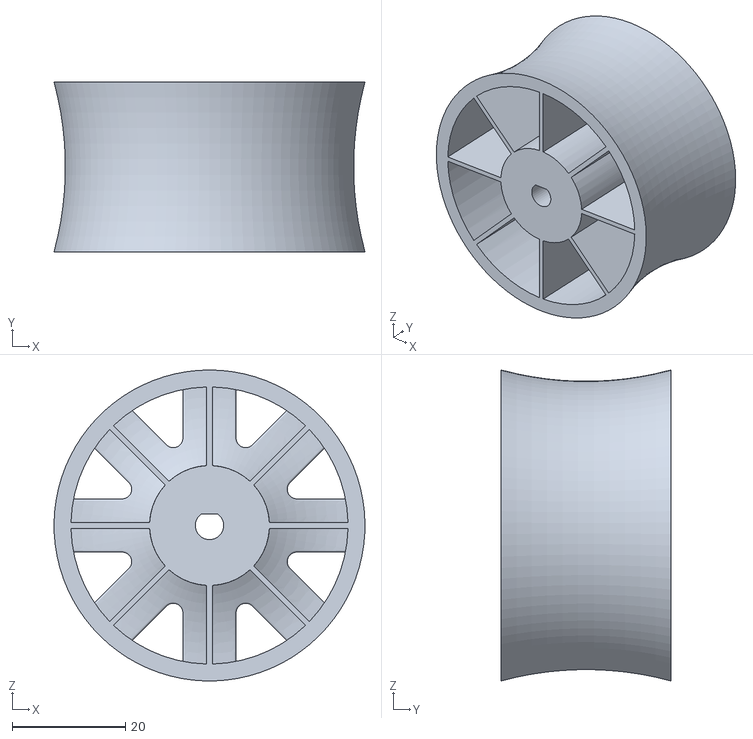
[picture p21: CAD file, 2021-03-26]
Projects/MonsterrhinoPrinterCar/3d_files/Rim.STL
55.0 x 30.0 x 55.0

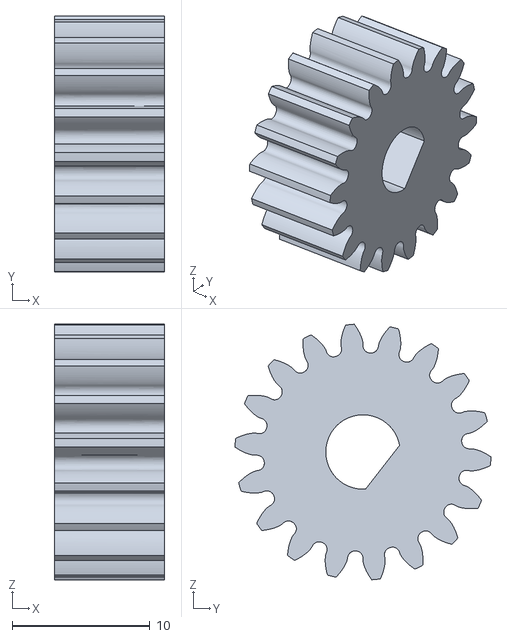
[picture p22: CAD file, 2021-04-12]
Projects/MonsterrhinoCameraSlider/3d_files/small_gear.stl
8.00 x 18.6 x 18.6

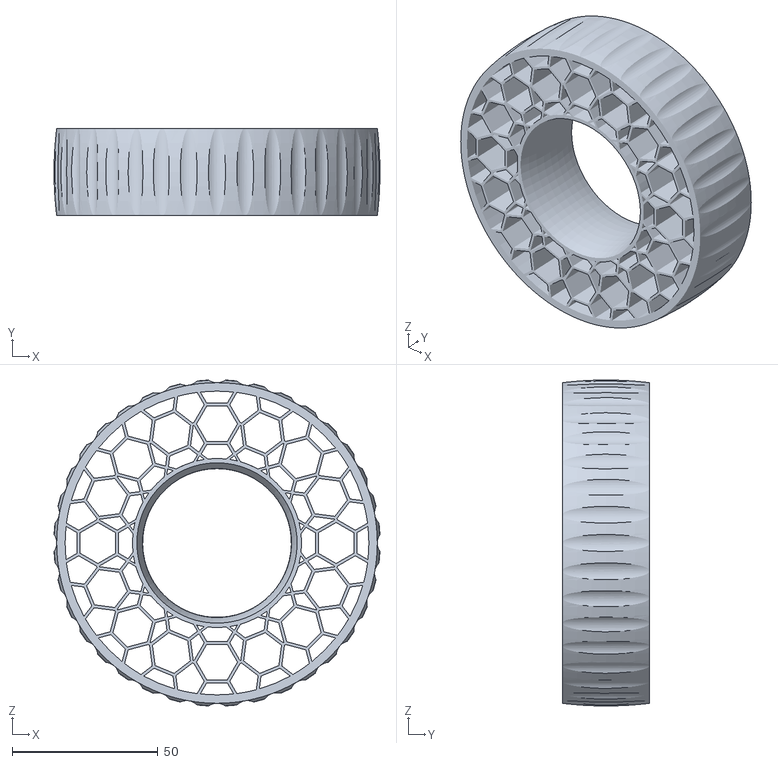
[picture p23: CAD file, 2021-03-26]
Projects/MonsterrhinoPrinterCar/3d_files/Tire.STL
111.8 x 30.0 x 111.8

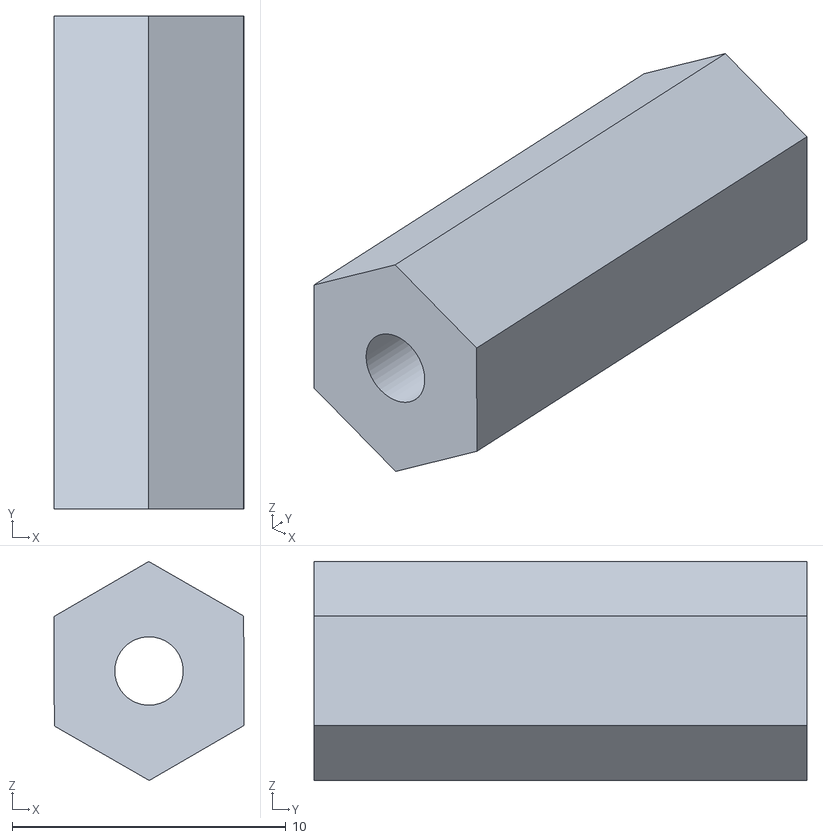
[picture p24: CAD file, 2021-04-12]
Projects/MonsterrhinoCameraSlider/3d_files/distance_rod.stl
6.94 x 18.0 x 8.00

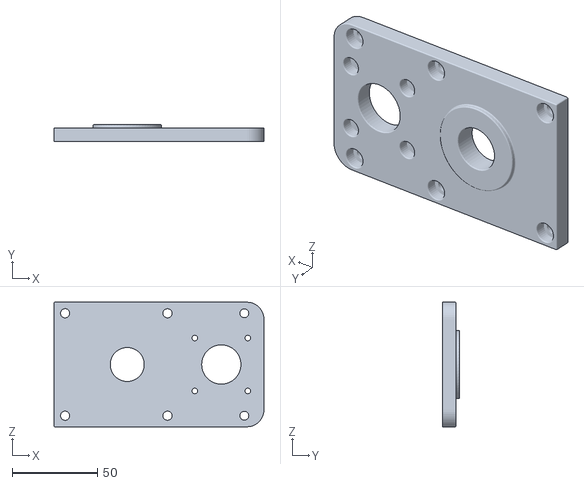
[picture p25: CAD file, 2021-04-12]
Projects/MonsterrhinoCameraSlider/3d_files/base_plate.stl
123.0 x 10.0 x 73.0

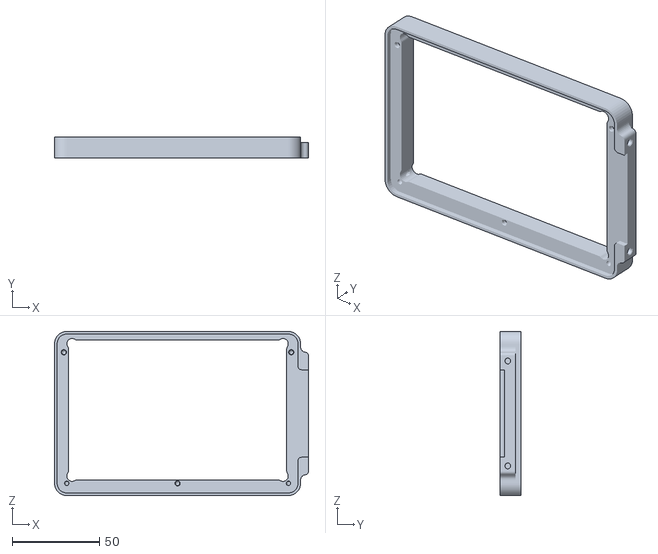
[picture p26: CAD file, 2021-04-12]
Projects/MonsterrhinoCameraSlider/3d_files/frame.stl
145.2 x 12.0 x 93.8

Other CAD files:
Projects/MonsterrhinoPrinterCar/3d_files/Chassis.STL
Projects/MonsterrhinoPrinterCar/3d_files/Chassis.x_t

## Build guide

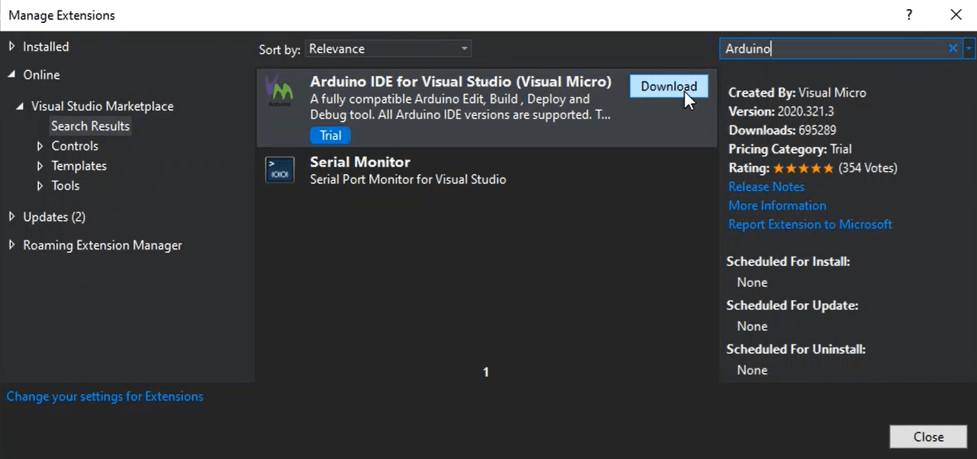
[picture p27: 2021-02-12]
Documentation/Images/Installation_VSGalleryDownload.png

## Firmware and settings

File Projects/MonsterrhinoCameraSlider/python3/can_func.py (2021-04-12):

'''
Author: Gregor Holzner
Company: Tratter Engineering SRL September 2020
Website: www.trattereng.com
'''

'''
Implementation protocol V2:
	-Addressing
		-Used frame format is extended (29 bit) Address 0-536.870.911
			
			
			
			
			
			- Bit 0-3 Nummer (0-15)
			- Bit 4-13	sub command (9 bit =512)	    ;select sub command
			- Bit 14-17	command (0-15)					;command
				0 ('s')									;Sytem
				1 ('m')									;Motor
				2 ('i')									;Input
				3 ('f')									;User function
			- Bit 18	error
			-Bit 19-23	to Address
				0										;is a Broadcast message				
				2-31									;to Address
			-Bit 24-28	from Address
				0										;Bus controller
				2-31									;from Address
			- Bit 29	dentifies respond message
				0										;respond message
				1										;send message
			- Address range:
				Address 0 = broadcast message
				Address 1 = Bus controller
				available address range for client is 2-31

		- get a value set RTR Bit in Can Protocol

	-Data Field
		-Byte MSB-0		user return function_ID (0-255)
						Bit 0-8 (0-127)					;return function_ID
			
		-Byte MSB-1 & MSB-7 <Data>		;length and type depending on the register


'''



from can import Message
from bitstring import BitStream, BitArray

def cmd_to_CAN(sub_command="0", motor_nr=1, usr_fnct_id=1, err=0, data=0, toAddress = 2, command="m", fromAddress = 1, respondMessage = 1):
        """
        Function to transform command into can frame to send it to monsterrhino
        :param cmd:
        :param sub_command:
        :param motor_nr:
        :param usr_fnct_id:
        :param err:
        :param data:
        :param toAddress:
        :param command:
        :param fromAddress:
        :param respondMessage:
        :return:
        """

        # error=0

        # c = fromAddress << 4

        # data field generation
        '''
        Byte MSB < command > (0 - 255) 'm/i/s/f'       command
		0 ('s') Sytem
		1 ('m')	Motor
		2 ('i') Input
		3 ('f') User function
        '''

        # print("Command: " + command)
        _cmd_list = ["s", "m", "i", "f"]

        try:
                command = [i for i, elem in enumerate(_cmd_list) if command in elem][0]
                # print("converted to " + str(command))
        except IndexError as error:
                print("ERROR: " + str(error))
                command = 0
        _subcmd_list = ["0","1","2","rm","tp", "cp", "mr","" ,"", "", "ms"]
        try:
                subCommand = [i for i, elem in enumerate(_subcmd_list) if sub_command in elem][0]
        except IndexError as error:
                print("ERROR: " + str(error))
                subCommand = 0
        # print("Subcommand converted to: " + str(subCommand))
        err=1
        address = (int(respondMessage) << 28) | ((int(fromAddress) & 0x1F) << 23) | ((int(toAddress) & 0x1F) << 18) | ((int(err) & 0x01) << 17) | ((int(command) & 0x0F) << 13) | ((int(subCommand) & 0x1F)) << 4 | ((int(motor_nr) & 0xF));

        '''
        -Byte MSB - 1 & MSB - 2 < subcommand > (12 bit); select sub function
        -Bit
        0 - 12(0 - 4095)				;subCommand
        "tp"    0
        "cp"    1
        "mo"    2
        "ms"    3
        '''

        _msb0 = usr_fnct_id

        # Byte MSB-4 to MSB-7 <Data>(32 bit)		;length and type depending on the register
        # print("data: " + str(data))
        if (data == "?"):
                data = 0
        data = int(data)
        _msb1 = data & int(0xFF)
        _msb2 = (data >> 8) & int(0xFF)
        _msb3 = (data >> 16) & int(0xFF)
        _msb4 = (data >> 24) & int(0xFF)
        _msb5 = 0
        _msb6 = 0
        _msb7 = 0
        data = [        _msb0,           # MSB
                        _msb1,          # MSB-1
                        _msb2,          # MSB-2
                        _msb3,          # MSB-3
                        _msb4,          # MSB-4
                        _msb5,          # MSB-5
                        _msb6,          # MSB-6
                        _msb7]          # MSB-7


        return address, data

def uf_to_CAN( fromAddress = 1, toAddress = 2, respondMessage = 1, usr_fnct_id = 1, command = "f", sub_command = "s", uf_nr = 6, par = 1):
        # data field generation
        '''
        -Byte MSB < command > (0 - 255) 'm/i/s/f'       ;command
        'm'		0						                ;Motor
        'i'		1							            ;Input
        's'		2							            ;Sytem
        'f'		3							            ;User function
        '''

        data = par

        # print("Command " + command + ":")
        _cmd_list = ["s", "m", "i", "f"]
        try:
                command = [i for i, elem in enumerate(_cmd_list) if command in elem][0]
        except IndexError as error:
                print("ERROR: " + str(error))
                command = 0

        # print(command)

        # print("Subcommand " + sub_command + ":")
        _subcmd_list = ["0", "s", "uvF1", "uv4", "uv5"]
        try:
                sub_command = [i for i, elem in enumerate(_subcmd_list) if sub_command in elem][0]
                # In case it is the uservariable float set to 40
                if sub_command == 2:
                        sub_command = 40
                if sub_command == 3:
                        sub_command = 33
                if sub_command == 4:
                        sub_command = 34

        except IndexError as error:
                print("ERROR: " + str(error))
                sub_command = 0

        # print(sub_command)

        err = 1
        address = (int(respondMessage) << 28) | ((int(fromAddress) & 0x1F) << 23) | ((int(toAddress) & 0x1F) << 18) | (
                        (int(err) & 0x01) << 17) | ((int(command) & 0x0F) << 13) | (int(sub_command) & 0x7F) << 4 | (
                  (int(uf_nr) & 0xF));

        '''
        -Byte MSB - 1 & MSB - 2 < subcommand > (12 bit); select sub function
        -Bit
        0 - 12(0 - 4095)				;subCommand
        "tp"    0
        "cp"    1
        "mo"    2
        "ms"    3
        '''
        _msb0 = usr_fnct_id

        # Byte MSB-4 to MSB-7 <Data>(32 bit)		;length and type depending on the register
        # data = 1

        # print("data: " + str(data))
        if (data == "?"):
                data = 0
        data = int(data)
        _msb1 = data & int(0xFF)
        _msb2 = (data >> 8) & int(0xFF)
        _msb3 = (data >> 16) & int(0xFF)
        _msb4 = (data >> 24) & int(0xFF)
        _msb5 = 0
        _msb6 = 0
        _msb7 = 0
        data = [_msb0,  # MSB
                _msb1,  # MSB-1
                _msb2,  # MSB-2
                _msb3,  # MSB-3
                _msb4,  # MSB-4
                _msb5,  # MSB-5
                _msb6,  # MSB-6
                _msb7]  # MSB-7

        return address, data

def uv_from_CAN( fromAddress = 1, toAddress = 2, respondMessage = 1, get_val = 128, command = 3, sub_command = 3, uf_nr = 6, data = 0):

        # data field generation
        '''
        -Byte MSB < command > (0 - 255) 'm/i/s/f'       ;command
        'm'		0						                ;Motor
        'i'		1							            ;Input
        's'		2							            ;Sytem
        'f'		3							            ;User function
        '''
        err = 1
        address = (int(respondMessage & int('1', 2)) << 28) |\
                  ((int(fromAddress) &  int('11111', 2)) << 23) | \
                  ((int(toAddress) &    int('11111', 2)) << 18) | \
                  ((int(err) &          int('1', 2)) << 17) | \
                  ((int(command) &      int('1111', 2)) << 13) | \
                  (int(sub_command) &   int('111111111', 2)) << 4 | \
                  ((int(uf_nr) &        int('1111', 2)));


        _msb0 = get_val #& int('00000001', 2)
        #print("msb0: " + str(_msb0))

        # Byte MSB-4 to MSB-7 <Data>(32 bit)		;length and type depending on the register
        # data = 1
        if (data == "?"):
                data = 0
        data = int(data)
        _msb1 = data & int(0xFF)
        _msb2 = (data >> 8) & int(0xFF)
        _msb3 = (data >> 16) & int(0xFF)
        _msb4 = (data >> 24) & int(0xFF)
        _msb5 = 0
        _msb6 = 0
        _msb7 = 0
        data = [_msb0,  # MSB
                _msb1, # MSB-1
                _msb2,  # MSB-2
                _msb3,  # MSB-3
                _msb4]  # MSB-4
                #_msb5,  # MSB-5
                #_msb6,  # MSB-6
                #_msb7]  # MSB-7

        # test = Message(is_extended_id=False, is_error_frame=False, arbitration_id=address, data=data)
        #print("Get uservariable...")
        return address, data

def sys_to_CAN(sub_command="sytemReboot", motor_nr=0, usr_fnct_id=0, err=0, data=0, toAddress = 2, command="s", fromAddress = 1, respondMessage = 0):
        """
        Function to transform command into can frame to send it to monsterrhino
        :param cmd:
        :param sub_command:
        :param motor_nr:
        :param usr_fnct_id:
        :param err:
        :param data:
        :param toAddress:
        :param command:
        :param fromAddress:
        :param respondMessage:
        :return:
        """

        '''
        Byte MSB < command > (0 - 255) 'm/i/s/f'       command
		0 ('s') Sytem
		1 ('m')	Motor
		2 ('i') Input
		3 ('f') User function
		
		
					- Bit 0-3 Nummer (0-15)
			- Bit 4-13	sub command (9 bit =512)	    ;select sub command
			- Bit 14-17	command (0-15)					;command
				0 ('s')									;Sytem
				1 ('m')									;Motor
				2 ('i')									;Input
				3 ('f')									;User function
			- Bit 18	error							; active low
			-Bit 19-23	to Address
				0										;is a Broadcast message				
				2-31									;to Address
			-Bit 24-28	from Address
				0										;Bus controller
				2-31									;from Address
			- Bit 29	dentifies respond message
				0										;respond message
				1										;send message
			- Address range:
				Address 0 = broadcast message
				Address 1 = Bus controller
				available address range for client is 2-31
				
		SubCommand_System:
		 systemSN = 1,						//
		 systemFirmareTime = 2,				//
		 sytemHV = 3,						//
		 sytemSV = 4,						//
		 sytemSaveConguration = 5,			//
		 sytemRestoreConguration = 6,		//
		 sytemDefaultConguration = 7,		//
		 sytemFactoryDefaultConguration = 8,//
		 sytemProgrammKey = 9,				//
		 sytemReboot = 10,					//
		 systemDebugLevel =11,				//
		 systemStartUpDebugLevel = 12,		//
		 systemCanAdd =13,					//
		 systemStartUpCanAdd = 14,			//
		 systemCanSpeed = 15,				//
		 systemStartUpCanSpeed =16,			//
		 systemDipSwitch=17,				//
		 systemDoor=18,						//
		 systemPWM=19,						//
		 systemStartUpPWM=20,
		 systemPWM_Frequency = 21,
		 systemStartUpPWM_Frequency = 22,
        '''

        # print("Command: " + command)
        _cmd_list = ["s", "m", "i", "f"]

        try:
                command = [i for i, elem in enumerate(_cmd_list) if command in elem][0]
                # print("converted to " + str(command))
        except IndexError as error:
                print("ERROR: " + str(error))
                command = 0
        _subcmd_list = ["","systemSN",	"systemFirmareTime", "sytemHV", "sytemSV", "sytemSaveConguration", "sytemRestoreConguration",
		 "sytemDefaultConguration", "sytemFactoryDefaultConguration", "sytemProgrammKey", "sytemReboot", "systemDebugLevel",
		 "systemStartUpDebugLevel", "systemCanAdd", "systemStartUpCanAdd", "systemCanSpeed", "systemStartUpCanSpeed",
		 "systemDipSwitch", "systemDoor", "systemPWM", "systemStartUpPWM", "systemPWM_Frequency", "systemStartUpPWM_Frequency"]

        try:
                subCommand = [i for i, elem in enumerate(_subcmd_list) if sub_command in elem][0]
        except IndexError as error:
                print("ERROR: " + str(error))
                subCommand = 0
        # print("Subcommand converted to: " + str(subCommand))
        err=1
        address = (int(respondMessage) << 28) | ((int(fromAddress) & 0x1F) << 23) | ((int(toAddress) & 0x1F) << 18) |\
                  ((int(err) & 0x01) << 17) | ((int(command) & 0x0F) << 13) | ((int(subCommand) & 0x1F)) << 4 | \
                  ((int(motor_nr) & 0xF));

        _msb0 = usr_fnct_id

        # Byte MSB-4 to MSB-7 <Data>(32 bit)		;length and type depending on the register
        # print("data: " + str(data))
        if (data == "?"):
                data = 0
        data = int(data)
        _msb1 = data & int(0xFF)
        _msb2 = (data >> 8) & int(0xFF)
        _msb3 = (data >> 16) & int(0xFF)
        _msb4 = (data >> 24) & int(0xFF)
        _msb5 = 0
        _msb6 = 0
        _msb7 = 0
        data = [        _msb0,           # MSB
                        _msb1,          # MSB-1
                        _msb2,          # MSB-2
                        _msb3,          # MSB-3
                        _msb4,          # MSB-4
                        _msb5,          # MSB-5
                        _msb6,          # MSB-6
                        _msb7]          # MSB-7

        return address, data

if __name__ == '__main__':

        # address, data = sys_to_CAN(sub_command="sytemReboot", motor_nr=0, usr_fnct_id=0, err=0, data=0, toAddress = 2, command="s", fromAddress = 1, respondMessage = 0)
        # print(address, data)

        print(int('110000', 2))

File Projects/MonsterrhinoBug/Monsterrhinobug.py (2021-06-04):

import tkinter as tk
from tkinter import *
from tkinter import ttk, Button, Label, Frame, OptionMenu, Text, filedialog
from math import pi, cos, sin
from PIL import Image, ImageTk
from tkinter import colorchooser
import threading
import serial
import glob
import numpy as np
import time

BUTTON_IMGS = ["images/rotate_bwd.png",     # 0
               "images/rotate_fwd.png",     # 1
               "images/step_bwd.png",       # 2
               "images/step_fwd.png",       # 3
               "images/tab1_active_old.png", # 4
               "images/stop.png",           # 5
               "images/color_btn.png",      # 6
               "images/on.png",             # 7
               "images/off.png"             # 8
               ]

class MyApp:
    def __init__(self):
        self.myContainer1 = tk.Tk()
        # self.myContainer1.wm_attributes('-type', 'splash')
        self.myContainer1.title("MonsterrhinoMotion Bug")
        self.myContainer1.geometry("800x480")
        self.myContainer1.configure(bg="black")
        self.speed = 200
        self._connected = False

        # Connect to serial port
        _temp_po = Image.open(BUTTON_IMGS[8])
        self._con_img = ImageTk.PhotoImage(_temp_po)
        self._con = Button(self.myContainer1, image=self._con_img, command=self.connect_to_serial_port)
        self._con.config(bg='black', fg="white", activebackground='black', borderwidth=0,
                                        highlightbackground="black", font="none 18")
        self._con.place(x=740, y=80, anchor="s")

        # Run left
        _temp_po = Image.open(BUTTON_IMGS[0])
        self._left_img = ImageTk.PhotoImage(_temp_po)
        self._left = Button(self.myContainer1, image=self._left_img, command=self.run_right)
        self._left.config(bg='black', fg="white", activebackground='black', borderwidth=0,
                                        highlightbackground="black", font="none 18")
        self._left.place(x=150, y=300, anchor="s")

        # Run right
        _temp_po = Image.open(BUTTON_IMGS[1])
        self._right_img = ImageTk.PhotoImage(_temp_po)
        self._right = Button(self.myContainer1, image=self._right_img, command=self.run_left)
        self._right.config(bg='black', fg="white", activebackground='black', borderwidth=0,
                                        highlightbackground="black", font="none 18")
        self._right.place(x=430, y=300, anchor="s")

        # Step forward
        _temp_po = Image.open(BUTTON_IMGS[3])
        self._fwd_img = ImageTk.PhotoImage(_temp_po)
        self._fwd = Button(self.myContainer1, image=self._fwd_img, command=self.run_backward)
        self._fwd.config(bg='black', fg="white", activebackground='black', borderwidth=0,
                                        highlightbackground="black", font="none 18")
        self._fwd.place(x=290, y=195, anchor="s")

        # Step backward
        _temp_po = Image.open(BUTTON_IMGS[2])
        self._bwd_img = ImageTk.PhotoImage(_temp_po)
        self._bwd = Button(self.myContainer1, image=self._bwd_img, command=self.run_straight)
        self._bwd.config(bg='black', fg="white", activebackground='black', borderwidth=0,
                                        highlightbackground="black", font="none 18")
        self._bwd.place(x=290, y=410, anchor="s")

        # Stop
        _temp_po = Image.open(BUTTON_IMGS[5])
        self._stop_img = ImageTk.PhotoImage(_temp_po)
        self._stop = Button(self.myContainer1, image=self._stop_img, command=self.stop)
        self._stop.config(bg='black', fg="white", activebackground='black', borderwidth=0,
                                        highlightbackground="black", font="none 18")
        self._stop.place(x=290, y=305, anchor="s")

        # Speed scale
        self._scale_label = Label(self.myContainer1)
        self._scale_label.config(text="Speed")
        self._scale_label.place(x=180, y=75, anchor="s")
        self._scale_label.config(bg='black', fg="white", activebackground='white', borderwidth=1,
               highlightbackground="black", font="none 18")

        self._scale = Scale(self.myContainer1, from_=0, to=300,
                                     orient=tk.HORIZONTAL)
        self._scale.set(200)
        self._scale.config(bg='black', fg="white", activebackground='black', borderwidth=0,
                                        highlightbackground="black", font="none 18", command=self.set_speed)
        self._scale.place(x=280, y=70, anchor="s")

        # Color
        _temp_po = Image.open(BUTTON_IMGS[6])
        self._color_img = ImageTk.PhotoImage(_temp_po)
        self._color = Button(self.myContainer1, image=self._color_img, text="Select color",
                        command=self.choose_color)
        self._color.config(bg='black', fg="white", activebackground='white', borderwidth=1,
                          highlightbackground="black", font="none 18")
        self._color.place(x=630, y=310, anchor="s")

        # Random color button
        self._rand_color = Button(self.myContainer1, text="Random color",
                        command=self.choose_color)
        self._rand_color.config(bg='black', fg="white", activebackground='white', borderwidth=1,
                          highlightbackground="black", font="none 18", command=self.random_color)
        self._rand_color.place(x=630, y=380, anchor="s")

        self.port_name_label = Label(self.myContainer1, text='Select port: ')
        self.port_name_label.config(bg='black', fg="white", activebackground='white', borderwidth=1,
                          highlightbackground="black", font="none 12")
        self.port_name_label.place(x=460, y=70, anchor="s")
        # creating a entry for input
        # name using widget Entry
        self.port_name_var = StringVar()

        self.ports_list = self.serial_ports()
        self.port_name_var.set(self.ports_list[0])
        print(self.serial_ports())
        self.name_entry = tk.OptionMenu(self.myContainer1, self.port_name_var, *self.ports_list)
        self.name_entry.config(bg='black', fg="white", activebackground='white', borderwidth=1,
                          highlightbackground="black", font="none 12")
        self.name_entry.place(x=600, y=75, anchor="s")


    def set_speed(self, par):
        print(self._scale.get())
        self.speed = self._scale.get()

    def random_color(self):
        color = list(np.random.choice(range(256), size=3))
        self.color( color[0], color[1], color[2])
        print("Update random color!")
        self.myContainer1.after(2000, self.random_color)

    def choose_color(self):
        # variable to store hexadecimal code of color
        self.color_code = colorchooser.askcolor(title="Choose color")
        self.r = int(self.color_code[0][0])
        self.g = int(self.color_code[0][1])
        self.b = int(self.color_code[0][2])
        print(self.r, self.g, self.b)
        self.color(self.r, self.g, self.b)
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

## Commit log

2021-03-25 changed current value
2021-03-26 add MonsterrhinoPrinterCar project
    [Chassis.STEP, Chassis.STL, Chassis.x_t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]
2021-03-26 add motor stall example
2021-03-30 add homing
2021-04-12 add slider
    [base_plate.stl, distance_rod.stl, frame.stl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]
2021-04-26 add base plate cover
    [monsterrhino_bottom_cover.stl]
2021-05-26 add serial connection description Arduino and Python
2021-07-07 added STM32CubeProgrammer Upload to GettingStarted-Readme
